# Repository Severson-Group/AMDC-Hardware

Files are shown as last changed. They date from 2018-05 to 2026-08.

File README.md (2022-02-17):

# Advanced Motor Drive Controller (AMDC) Hardware

*The Advanced Motor Drive Controller (AMDC) is an open-source project from the [Severson Research Group](https://severson.wempec.wisc.edu/) at [UW-Madison](http://www.engr.wisc.edu/department/electrical-computer-engineering/), affiliated with [Wisconsin Electric Machines and Power Electronics Consortium (WEMPEC)](https://wempec.wisc.edu/).*

Learn more at [docs.amdc.dev](https://docs.amdc.dev/).

---

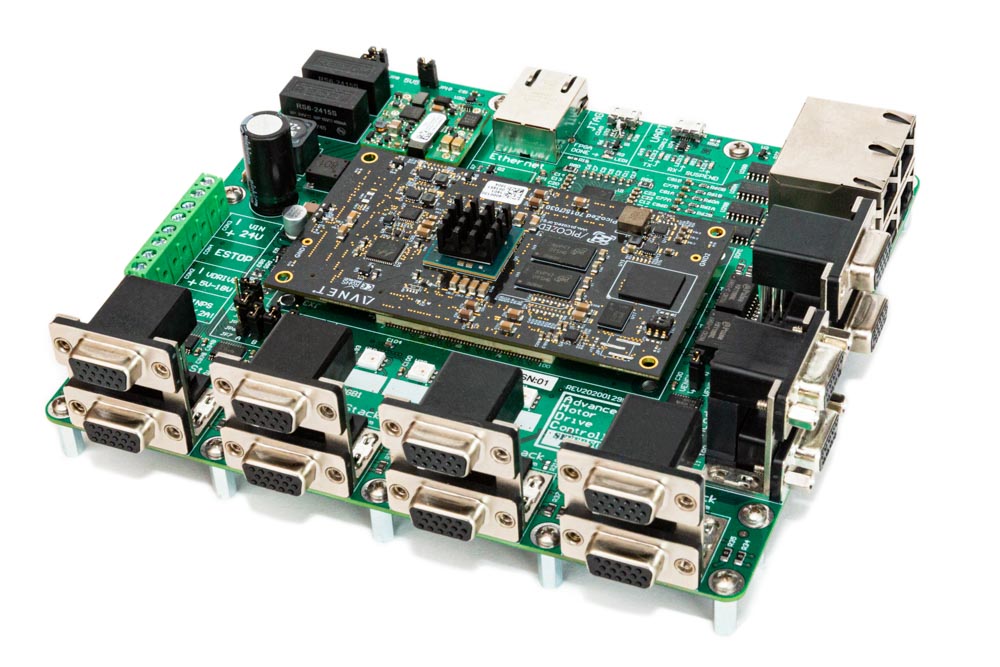
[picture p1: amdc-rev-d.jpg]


**AMDC-Hardware** is a collection of circuit board designs which are used to control advanced motor systems. The hardware design is open-source, modular, and research-oriented.

The flagship circuit board is the main AMDC (see latest design [here](https://github.com/Severson-Group/AMDC-Hardware/tree/develop/REV20210325E)) which is a carrier board for the [PicoZed System-on-Module](https://www.avnet.com/wps/portal/us/products/avnet-boards/avnet-board-families/picozed/). The PicoZed is a module itself which contains the core requirements for the [Xilinx Zynq-7000](https://www.xilinx.com/products/silicon-devices/soc/zynq-7000.html) System-on-Chip. The Xilinx Zynq-7000 SoC is a powerful processor with dual-core DSPs and a tightly integrated FPGA.

Extensive firmware support is provided in the [AMDC-Firmware](https://github.com/Severson-Group/AMDC-Firmware) repo which targets this architecture.

## Repository Structure

The `altium` directory contains all files pertaining to schematics / board design in Altium Designer. These files should be the latest working copy of the project.

The `REVyyyymmdd*` directories represent snapshots of the project that were used to produce a physical PCB. These directories contain the *Gerber*, *Drill* (Excellon format), *Bill of Materials* (CSV), and *Schematic* (PDF) files.
- `REV` indicates a revision of design for manufacturing
- `yyyymmdd` indicates the date on which design was frozen
- `*` (letter) indicates which revision in sequence (A - first, B - second, etc.)

### Accessory Boards

Numerous accessory circuit boards are designed to work with the AMDC (e.g., DAC, TestBoard, CAN expansion, I/O expansion).

These are located in the [`/Accessories/`](https://github.com/Severson-Group/AMDC-Hardware/tree/develop/Accessories) subfolder. Each accessory board follows the same repo set-up conventions as desribed above for the main AMDC.

## Interfaces

The AMDC is designed for research environments where flexible and plentiful I/O are required.

The provided interfaces include:
- 48 digital output channels (designed to provide PWM signals for 8 three phase, two level inverters)
- 8 analog input channels (+/- 10V differential input)
- 4 GPIO expansion ports (differential I/O)
- 2 quadrature encoder input

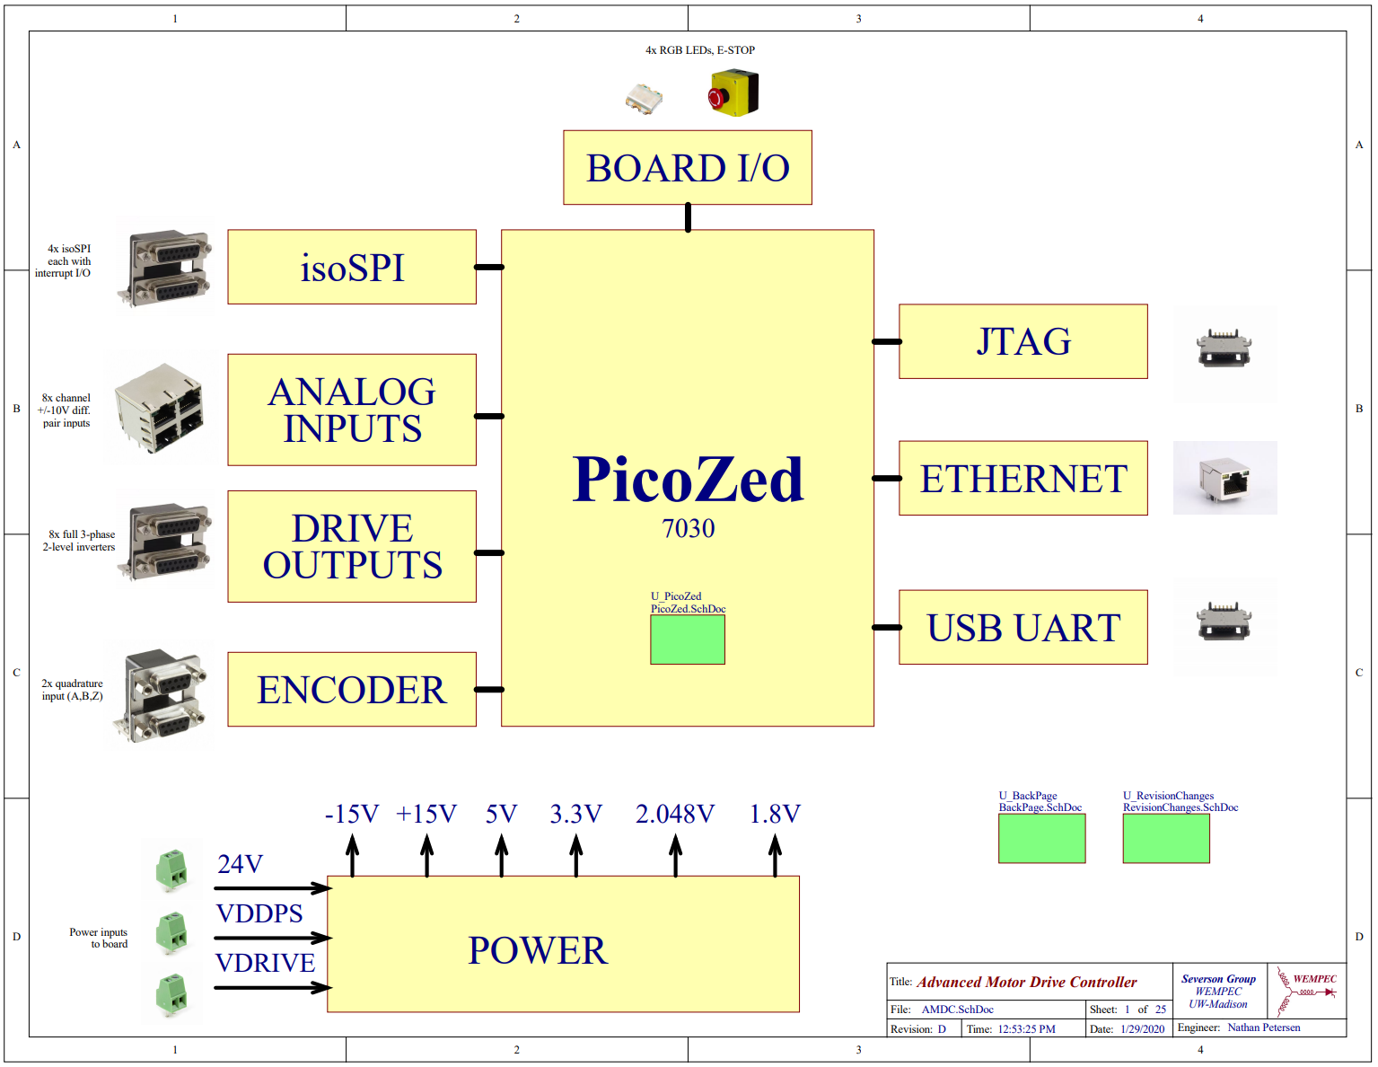
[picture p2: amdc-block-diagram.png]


## Getting Started

The AMDC-Hardware project is open-source -- contributors are welcome!

### Ordering Hardware

The `REVxxxx/` output folder contains the compiled design files needed to order hardware:
1. Review the board design using the 3D renderings and the schematics PDF
2. Check the `docs/` folder for any imformation about the board design
3. Order PCB blanks using the gerber files in the `REVxxxx/gerbers/` folder and the specs provided in the `README.md` file
4. Order components using the BOM file provided as CSV

### Designing Modifications

Note: all board designs are created using Altium Designer -- a license is required to design boards for the AMDC-Hardware project.

The `altium/` subfolder contains the latest design files for the board.

## Documentation

Detailed documentation about the hardware is available online at: [docs.amdc.dev/hardware](https://docs.amdc.dev/hardware/).

The documentation explains the design narrative and process, design choices, requirements, relevant equations and diagrams, etc.

## Background

This project originated as [Nathan Petersen's](https://github.com/npetersen2) Independent Study project during Spring 2018, advised by Prof. Eric Severson. It is now actively maintained by the [Severson Research Group](http://severson.wempec.wisc.edu/). Open source firmware is available on GitHub in the [AMDC-Firmware](https://github.com/Severson-Group/AMDC-Firmware) repository.

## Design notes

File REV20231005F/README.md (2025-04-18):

# AMDC REV20231010F

This folder contains the compiled design outputs for AMDC REV F. This includes the schematics, images of the PCB layout, the bill of materials (BOM), and the files needed to order fully populated boards from an online vendor.

## Board Parameters

| Question | Answer |
|---|---|
| Board Size | 6" x 6.75" |
| Numer of Layers | 6 Layers |
| Double Sided | Yes |
| Surface Finish | Tin Lead |
| Silkscreen | White |
| Material | FR-4, TG150 |
| Board Thickness | 1.6 mm |
| Min Trace Spacing | 0.15 mm (6 mil)  |
| Min Hole Size | 0.36 mm (14 mil) |
| Number of Holes | 1528 |
| Solder Mask | Green |
| HASL or ENIG | No |
| Finished Copper | 1 oz |

## Assembly Details

| Question[^1] | Answer |
|---|---|
| Unique Part Count[^2] | 67 |
| Number of Total Parts[^2] | 447 |
| Total SMT Part Count | 415 |
| Total Through-hole Part Count | 32 |
| Total Mechanical Screws | 13 |
| Total Mechanical Standoffs | 13 |
| Total Removable Jumpers | 10 |
| Total Picozed | 1 |
| BGA / QFN | Yes |

## Bill of Materials

The [Bill of Materials (BOM)](bom-rev-f.csv) contains components for 1 board. If users of this repo discover that any components are unvailable, please maintain an `alternate-components.md` file in this folder that lists approved alternates.

[^1]: For complete breakdown of surface mount, through-hole, and other components, see [this pull request comment](https://github.com/Severson-Group/AMDC-Hardware/pull/255#issuecomment-2815977355)

[^2]: This number does not include screws, standoffs, removable jumpers, or the picozed. With these components included, the unique part count is 71 and total parts is 484. Users are advised to not have their assembly vendor place these components.

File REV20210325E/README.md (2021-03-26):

# AMDC REV20210325E

This folder contains the compiled design outputs for AMDC REV E (design frozen on March 25, 2021). This includes the schematics, images of the PCB layout, the bill of materials (BOM), and the files needed to order fully populated boards from an online vendor.

## Board Parameters

| Question | Answer |
|---|---|
| Unique Part Count | 69 |
| Total Placements | 472 |
| Total SMT Part Count | 439 |
| Total SOP/QFP/QFN/BGA | 52 |
| Total Thru Hole Part Count | 32 |
| BGA / QFN | Yes |
| Double Sided | Yes |

| Question | Answer |
|---|---|
| Board Size (H x W) | 6" x 6.75"  |
| Numer of Layers | 6 |
| Number of Holes | 1519 |
| Number of Slots/Cutouts | 0 |
| Surface Finish | Tin Lead |
| Silkscreen | Both Sides  |
| Electrical Test | Yes |

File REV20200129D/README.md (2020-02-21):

# AMDC REV20200129D

This folder contains the compiled design outputs for AMDC REV D (design frozen on Jan 29, 2020). This includes the schematics, images of the PCB layout, the bill of materials (BOM), and the files needed to order fully populated boards from Screaming Circuits.

## How do I order more REV D AMDCs?

All the files required for placing an order of REV D AMDCs reside in this folder. The following steps outline the ordering procedure with answers to the questions asked by Screaming Circuits. We will assume ordering 10 qty.

1. Go to [Screaming Circuits website](https://www.screamingcircuits.com/).
2. Start a new online quote.
3. Fill out `Assembly Quote` section

| Question | Answer |
|---|---|
| Quantity | 10 |
| Unique Part Count | 64 |
| Total Placements | 366 |
| Thru Hole Placements | 27 |
| BGA / QFN | Yes |
| Double Sided | Yes, SMT |
| RoHS | No |
| Class III | No |
| ITAR | No |

4. Fill out `PCB Fabrication Quote` section

| Question | Answer |
|---|---|
| Board Size (H x W) | 6" x 6.75"  |
| Numer of Layers | 6 |
| Number of Holes | 1387 |
| Number of Slots/Cutouts | 0 |
| Surface Finish | Tin Lead |
| Silkscreen | Both Sides  |
| Electrical Test | Yes |

5. Fill out `Parts Quote` section
    1. Upload the BOM from the `ScreamingCircuits/` folder.
    2. Wait for website to parse file... takes ~1 minute...
    3. Look for parts that they cannot source (out of stock, etc) -- this is usually fine, but make sure!
    3. Click `SAVE CHANGES`.

6. Select `Pricing` option and click `CHECK OUT`.
7. Name the project: "AMDC" and "REV20200129D" are logical.
8. Upload a ZIP file of the `ScreamingCircuits` folder for the "Project Files" section.
9. Fill out contact info, shipping info, and billing info.
10. Pay for order and wait for AMDCs to arrive!

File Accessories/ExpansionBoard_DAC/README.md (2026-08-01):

# AMDC DAC Expansion Board

The AMDC DAC expansion board is an accessory for the AMDC Rev E which provides 8 analog outputs (+- 10V output). The expansion board plugs into the AMDC via the Power Stack or GPIO interfaces.

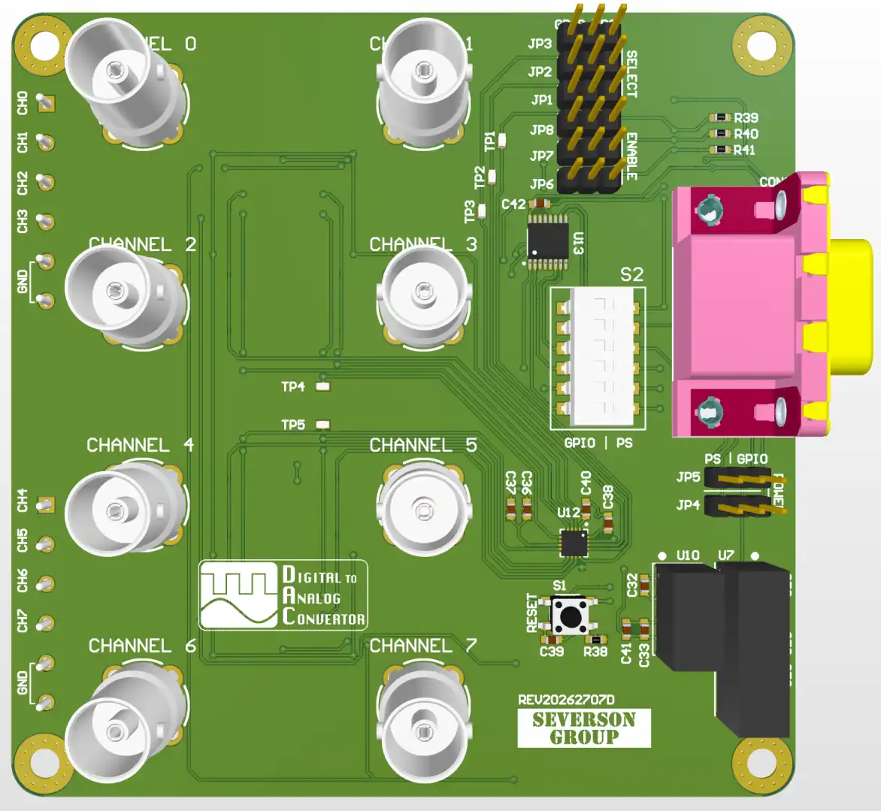
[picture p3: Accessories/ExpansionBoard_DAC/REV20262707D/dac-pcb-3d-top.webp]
PCD_3D


## Documentation

Documentation about the design of this expansion board is located at [docs.amdc.dev/accessories/dac/](https://docs.amdc.dev/main/accessories/dac/index.html).

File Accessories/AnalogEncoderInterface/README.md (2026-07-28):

# Analog Encoder Interface Board

This subfolder houses all the design files for the Analog Encoder Interface board. This board plugs into the AMDC analog inputs via ethernet cables.

## Documentation

Read about the design of this board on [docs.amdc.dev](docs.amdc.dev/main/accessories/analog-encoder).

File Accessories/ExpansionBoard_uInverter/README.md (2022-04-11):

# uInverter Board

The uInverter (micro-inverter) board is an accessory for the AMDC. The purpose of this board is to serve as a low-cost, micro-level prototype board to demonstrate three-phase current regulation using the AMDC. It uses a 12V DC supply to drive a three phase RL load circuit to emulate a motor.   

## Features:    
- Three phase AC current and DC bus voltage sensing feedback to AMDC.   
- Test points to measure voltages at various locations in the supply as well as load circuits.   
- BNC connector to directly measure the current waveforms on an oscilloscope conveniently.    

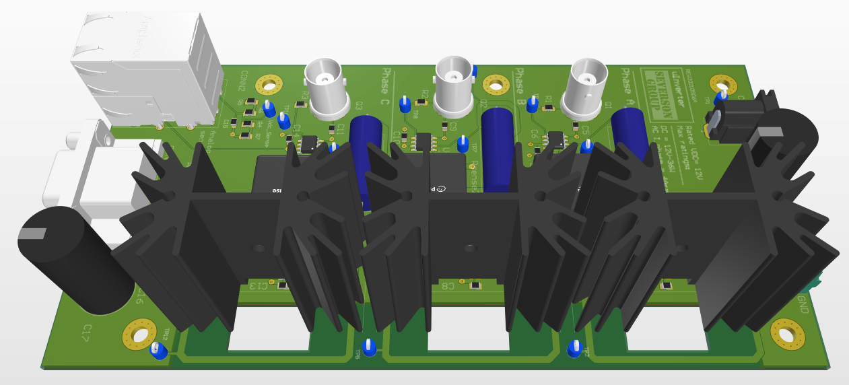
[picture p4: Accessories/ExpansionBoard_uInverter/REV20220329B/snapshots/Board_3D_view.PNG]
PCB 3D


## Documentation

Detailed documentation about the uInverter board is available online at: [docs.amdc.dev/accessories/uinverter](https://docs.amdc.dev/accessories/uinverter/index.html).

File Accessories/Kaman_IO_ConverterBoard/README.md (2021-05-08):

# Kaman IO Converter Board

The Kaman I/O Converter board is an accessory for the AMDC Rev D which converts the 4 differential I/O from the IsoSPI port on the AMDC to single ended I/O specifically for the Kaman KD-5690-FE eddy current sensor. The converter board plugs into the AMDC via the IsoSPI interface. 

## Documentation

Documentation about the design of this board is located in then [docs folder.](docs/)

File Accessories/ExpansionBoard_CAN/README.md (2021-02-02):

# AMDC CAN Expansion Board

The AMDC CAN expansion board is an accessory to the AMDC REVD with the goal of providing the AMDC the ability to interface with CAN devices. 

## Documentation
Documentation about the design of this expansion board can be found in the [docs folder.](docs/)

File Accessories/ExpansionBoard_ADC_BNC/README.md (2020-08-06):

# AMDC Expansion Board: Analog Inputs to BNC

This subfolder houses all the design files for the AMDC analog to BNC expansion board. This board plugs into the AMDC analog inputs via four ethernet cables.

## Documentation

Read about the design of this board in the [`docs/` folder](docs/).

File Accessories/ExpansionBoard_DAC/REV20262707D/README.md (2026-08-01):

# AMDC DAC Expansion Board REV20262707D

This folder contains the compiled design outputs for the AMDC DAC Expansion Board REV D. This includes the schematics, images of PCB layout, the bill of materials (BOM), and the files needed to order PCBs from online vendors.

## Board Parameters

| Question | Answer |
|---|---|
| Board Size | 3.91" x 3.91" |
| Number of Layers | 2 Layers |
| Double Sided | Yes |
| Surface Finish | Tin lead |
| Silkscreen | White (both sides) |
| Material | FR-4 |
| Board Thickness | 1.6 mm |
| Min Trace Spacing | 0.152 mm (6 mil) |
| Min Hole Size | 0.36 mm (14 mil) |
| Number of Holes | 233 |
| Solder Mask | Green |
| HASL or ENIG | HASL |
| Finished Copper | 1 oz |

## Assembly Details

| Question | Answer |
|---|---|
| Unique Part Count[^1] | 27 |
| Number of Total Parts[^1] | 117 |
| Total SMT Part Count | 96 |
| Total Through-hole Part Count | 21 |
| Total Mechanical Screws | 4 |
| Total Mechanical Standoffs | 4 |
| Total Jumper Connectors | 8 |
| BGA / QFN | QFN (U12) |

## Bill of Materials

The [Bill of Materials (BOM)](./dac-rev-d-bom.csv) contains components for 1 board. If users of this repo discover that any components are unavailable, please maintain an `alternate-components.md` file in this folder that lists approved alternates.

[^1]: This number does not include screws, standoffs, or jumper connectors. With screws, standoffs, and jumper connectors included, the unique part count is 30 and total parts is 133. Users are advised to not have their assembly vendor place screws, standoffs, and jumper connectors.

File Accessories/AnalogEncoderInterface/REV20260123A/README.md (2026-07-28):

# Analog Encoder Interface Board REV20260123A
This folder contains the compiled design outputs for the Analog Encoder Interface Board REVA. This includes the schematics, images of PCB layout, the bill of materials (BOM), and the files needed to order PCBs from online vendors.

## Analog Encoder Interface Board

| Question | Answer |
|---|---|
| Board Size | 73mm x 80mm |
| Number of Layers | 4 Layers |
| Double Sided | Yes |
| Surface Finish | Tin Lead |
| Silkscreen | White |
| Material | FR-4, TG150 |
| Board Thickness | 1.6 mm (62 mil) |
| Min Trace Spacing | 0.2 mm (7.9 mil)  |
| Min Hole Size | 0.3 mm (11.8 mil) |
| Number of Holes | 63 |
| Solder Mask | Purple |
| HASL or ENIG | No |
| Inner Copper | 1 oz |
| Outer Copper | 1 oz |

### Assembly Details

| Question | Answer |
|---|---|
| Unique Part Count | 20 |
| Number of Total Parts | 57 |
| Total SMD Part Count | 24 |
| Total Through-hole Part Count  | 25 |
| Total Mechanical Screws | 4 |
| Total Mechanical Standoffs | 4 |
| BGA / QFN | No |

## Bill of Materials

The [Bill of Materials (BOM)](aei-bom.csv) contains components for 1 of each board.

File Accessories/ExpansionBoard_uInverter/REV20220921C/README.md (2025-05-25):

# uInverter Board

This folder contains the compiled design outputs for the uInverter expansion board. This includes schematics, images of the PCB layout, the bill of materials (BOM) and the files needed to order boards from an online vendor. 

## Board Parameters

| Question | Answer |
|---|---|
| Board Size | 3.5" x 6.9" |
| Number of Layers  | 2 Layers |
| Double Sided | No |
| Surface Finish | Tin lead |
| Silkscreen | White |
| Material | FR-4, TG150 |
| Board Thickness | 1.6mm |
| Min Track/Spacing | 0.15 mm (6 mil) |
| Min Hole Size | 0.38 mm (15 mil)  |
| Number of holes | 198 |
| Solder Mask | Black |
| HASL or ENIG | No |
| Finished Copper | 1 oz |

## Assembly Details

| Question | Answer |
|---|---|
| Unique Part Count[^1] | 19 |
| Number of Total Parts[^1] | 61 |
| Total SMT Part Count | 33 |
| Total Through-hole Part Count | 28 |
| Total Mechanical Components | 28 |
| BGA / QFN | No |

## Bill of Materials

The [Bill of Materials (BOM)](uinv-rev-c-bom.csv) contains components for 1 board. If users of this repo discover that any components are unavailable, please maintain an `alternate-components.md` file in this folder that lists approved alternates.

[^1]: This number does not include mechanical components. With mechanical components included, the unique part count is 27 and total parts is 89. Users are advised to not have their assembly vendor place screws and standoffs.

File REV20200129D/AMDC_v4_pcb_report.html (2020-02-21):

Altium customize

# Board Information Report

Date: | | 1/29/2020
Time: | | 1:09:38 PM
Elapsed Time: | | 00:00:01
Filename: | | C:\Users\Nathan\Documents\GitHub\AMDC-Hardware\altium\PCB_v4.PcbDoc
Units: | | mmmils

## Contents

Contents

Board Specification

General

Routing

Routing Information

Layer Information

Layer Information

Drill Pairs

Board Holes

Non-Plated Hole Size

Plated Hole Size

Board Slots

Non-Plated Slot Size

Plated Slot Size

Board Square Holes

Non-Plated Square Hole Size

Plated Square Hole Size

Other

Top Layer Annular Ring Size

Mid Layer Annular Ring Size

Bottom Layer Annular Ring Size

Pad Solder Mask

Pad Paste Mask

Pad Pwr/Gnd Expansion

Pad Relief Conductor Width

Pad Relief Air Gap

Pad Relief Entries

Via Solder Mask

Via Pwr/Gnd Expansion

Track Width

Arc Line Width

Arc Radius

Arc Degrees

Text Height

Text Width

Net Track Width

Net Via Size

## Board Specification

General
Board Size | 6750mils x 6000mils
Components on board | 408

Back to top

## Routing

Routing Information
Routing completion | 100.00%
Connections | 1700
Connections routed | 1700
Connections remaining | 0

Back to top

## Layer Information

Layer | Arcs | Pads | Vias | Tracks | Texts | Fills | Regions | ComponentBodies
Top Layer | 11 | 960 | 0 | 2439 | 0 | 0 | 140 | 0
Int1 (GND) | 0 | 0 | 0 | 0 | 0 | 0 | 1 | 0
Int2 (Sign) | 276 | 0 | 0 | 1094 | 0 | 0 | 0 | 0
Int3 (Sign) | 0 | 0 | 0 | 703 | 0 | 0 | 0 | 0
Int4 (PWR) | 0 | 0 | 0 | 192 | 0 | 0 | 1 | 0
Bottom Layer | 10 | 907 | 0 | 2742 | 0 | 0 | 159 | 0
Mechanical 15 | 0 | 0 | 0 | 569 | 0 | 0 | 0 | 6
Mechanical 13 | 46 | 0 | 0 | 384 | 0 | 0 | 0 | 81
Mechanical 12 | 0 | 0 | 0 | 20 | 0 | 0 | 0 | 11
Mechanical 1 | 1 | 0 | 0 | 0 | 0 | 0 | 0 | 277
Multi-Layer | 0 | 489 | 898 | 0 | 0 | 0 | 1 | 0
Drill Guide | 0 | 0 | 0 | 0 | 0 | 0 | 0 | 0
Keep-Out Layer | 4 | 0 | 0 | 4 | 0 | 0 | 0 | 0
Drill Drawing | 0 | 0 | 0 | 0 | 0 | 0 | 0 | 0
Top Paste | 0 | 0 | 0 | 0 | 0 | 0 | 0 | 0
Top Overlay | 44 | 0 | 0 | 6536 | 511 | 4 | 1 | 0
Top Solder | 0 | 0 | 0 | 0 | 0 | 0 | 0 | 0
Bottom Solder | 0 | 0 | 0 | 0 | 0 | 0 | 0 | 0
Bottom Overlay | 61 | 0 | 0 | 325 | 403 | 0 | 0 | 0
Bottom Paste | 0 | 0 | 0 | 0 | 0 | 0 | 0 | 0
Total | 453 | 2356 | 898 | 15008 | 914 | 4 | 303 | 375

Back to top

Drill Pairs | Vias
Top Layer - Bottom Layer | 898
Total | 898

Back to top

## Board Holes

Non-Plated Hole Size | Pads | Vias
32.008mils | 3 | 0
47.992mils | 3 | 0
Total | 6 | 0

Back to top

Plated Hole Size | Pads | Vias
0mils | 1867 | 0
12mils | 156 | 0
13.5mils | 0 | 7
14mils | 0 | 809
20mils | 0 | 79
30mils | 0 | 2
35mils | 32 | 0
35.039mils | 12 | 0
39.016mils | 2 | 0
39.37mils | 16 | 0
40mils | 0 | 1
40.158mils | 25 | 0
43.307mils | 18 | 0
44mils | 150 | 0
47.244mils | 6 | 0
50mils | 5 | 0
50.984mils | 2 | 0
51.181mils | 8 | 0
62mils | 6 | 0
125mils | 4 | 0
125.984mils | 4 | 0
126mils | 20 | 0
127.953mils | 2 | 0
128mils | 2 | 0
150mils | 13 | 0
Total | 2350 | 898

Back to top

## Board Slots

Non-Plated Slot Size / Length | Pads
Total | 0

Back to top

Plated Slot Size / Length | Pads
Total | 0

Back to top

## Board Square Holes

Non-Plated Square Hole Size | Pads
Total | 0

Back to top

Plated Square Hole Size | Pads
Total | 0

Back to top

## Other

Top Layer Annular Ring Size | Count
-2.008mils | 3
-2.008mils | 3
-0.047mils | 2
0mils | 2
12mils | 809
12.5mils | 7
14.961mils | 12
18mils | 156
19.685mils | 18
19.843mils | 25
20mils | 229
20.984mils | 2
23.622mils | 16
25mils | 32
26.583mils | 4
27.559mils | 8
27.756mils | 2
30mils | 2
39.37mils | 4
40mils | 8
45mils | 4
47.244mils | 6
54mils | 20
150mils | 13
Total | 1387

Back to top

Mid Layer Annular Ring Size | Count
-2.008mils | 3
-2.008mils | 3
-0.047mils | 2
0mils | 2
12mils | 809
12.5mils | 7
14.961mils | 12
18mils | 156
19.685mils | 18
19.843mils | 25
20mils | 229
20.984mils | 2
23.622mils | 16
25mils | 32
26.583mils | 4
27.559mils | 8
27.756mils | 2
30mils | 2
39.37mils | 4
40mils | 8
45mils | 4
47.244mils | 6
54mils | 20
150mils | 13
Total | 1387

Back to top

Bottom Layer Annular Ring Size | Count
-2.008mils | 3
-2.008mils | 3
-0.047mils | 2
0mils | 2
12mils | 809
12.5mils | 7
14.961mils | 12
18mils | 156
19.685mils | 18
19.843mils | 25
20mils | 229
20.984mils | 2
23.622mils | 16
25mils | 32
26.583mils | 4
27.559mils | 8
27.756mils | 2
30mils | 2
39.37mils | 4
40mils | 8
45mils | 4
47.244mils | 6
54mils | 20
150mils | 13
Total | 1387

Back to top

Pad Solder Mask | Count
1.969mils | 53
2mils | 64
2.5mils | 2201
2.953mils | 25
19.685mils | 13
Total | 2356

Back to top

Pad Paste Mask | Count
0mils | 2356
Total | 2356

Back to top

Pad Pwr/Gnd Expansion | Count
10mils | 2356
Total | 2356

Back to top

Pad Relief Conductor Width | Count
6mils | 2356
Total | 2356

Back to top

Pad Relief Air Gap | Count
6mils | 2356
Total | 2356

Back to top

Pad Relief Entries | Count
4 | 2356
Total | 2356

Back to top

Via Solder Mask | Count
2.5mils | 898
Total | 898

Back to top

Via Pwr/Gnd Expansion | Count
10mils | 898
Total | 898

Back to top

Track Width | Count
0.5mils | 4571
1mils | 1454
1.969mils | 320
3.937mils | 608
6mils | 3530
7mils | 2
7.874mils | 310
8mils | 347
10mils | 2567
12mils | 242
19.685mils | 1
20mils | 376
30mils | 515
40mils | 2
50mils | 129
75mils | 15
80mils | 16
100mils | 3
Total | 15008

Back to top

Arc Line Width | Count
3.937mils | 60
4mils | 8
8mils | 276
9.843mils | 60
10mils | 11
12mils | 4
18mils | 4
19.685mils | 1
23.622mils | 29
Total | 453

Back to top

Arc Radius | Count
1.969mils | 1
4.6mils | 8
4.921mils | 60
5.4mils | 144
6mils | 4
9mils | 17
9.843mils | 1
10.8mils | 12
11.811mils | 29
15.748mils | 1
19.685mils | 45
28.8mils | 12
30.067mils | 43
30.366mils | 1
31.441mils | 1
39.37mils | 13
48.067mils | 40
48.366mils | 1
49.441mils | 1
57.554mils | 1
80mils | 4
150mils | 8
175mils | 4
250mils | 2
Total | 453

Back to top

Arc Degrees | Count
0 | 2
1 | 1
23 | 2
32 | 11
45 | 1
68 | 1
70 | 1
72 | 2
75 | 1
76 | 2
77 | 36
90 | 178
91 | 2
113 | 2
121 | 1
122 | 9
132 | 1
139 | 1
142 | 1
145 | 3
150 | 1
154 | 21
176 | 1
360 | 172
Total | 453

Back to top

Text Height | Count
15mils | 1
30mils | 18
40mils | 428
50mils | 19
60mils | 428
70mils | 1
80mils | 16
125mils | 1
393.701mils | 2
Total | 914

Back to top

Text Width | Count
4mils | 1
5mils | 18
6mils | 12
10mils | 845
12mils | 8
15mils | 24
20mils | 6
Total | 914

Back to top

Net Track Width | Count
6mils | 461
10mils | 44
Total | 505

Back to top

Net Via Size | Count
22mils | 505
Total | 505

Back to top

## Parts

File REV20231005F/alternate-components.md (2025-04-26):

# Alternate Components

**A table of acceptable replacement components for the AMDC REV20231005F**

##

| Designator | Description | Original Part Number | Approved Alternate Part Numbers |
|---|---|---|---|
| HEATSINK1 | Heat Sink BGA Aluminum Top Mount | [1528-1697-ND](https://www.digikey.com/en/products/detail/adafruit-industries-llc/3083/6058478) | [684-ATS014014007-SF-3F-ND](https://www.digikey.com/en/products/detail/advanced-thermal-solutions-inc/ATS014014007-SF-3F/18711115) |
| C80 | CAP ALUM 100UF 20% 35V SMD | [493-2203-6-ND](https://www.digikey.com/en/products/detail/nichicon/UWT1V101MCL1GS/589944) | [493-6338-1-ND](https://www.digikey.com/en/products/detail/nichicon/UWZ1V101MCL1GS/2550909) |
| U7 | DC DC CONVERTER 24V 6W | [102-PQQ6W-Q24-S24-S-ND](https://www.digikey.com/en/products/detail/cui-inc/PQQ6W-Q24-S24-S/13402043) | [2725-URB2424S-6WR3-ND](https://www.digikey.com/en/products/detail/mornsun-america-llc/URB2424S-6WR3/13168170) <br> [4457-PDL06-24S24W-ND](https://www.digikey.com/en/products/detail/p-duke-technology/PDL06-24S24W/13531900) |
| Q3 | MOSFET 2N-CH 60V 5.3A 8SOIC | [SI4946CDY-T1-GE3DKR-ND](https://www.digikey.com/en/products/detail/vishay-siliconix/SI4946CDY-T1-GE3/7915484)| [SI4900DY-T1-GE3CT-ND](https://www.digikey.com/en/products/detail/vishay-siliconix/SI4900DY-T1-GE3/2622306) <br> [SI9945BDY-T1-GE3CT-ND](https://www.digikey.com/en/products/detail/vishay-siliconix/SI9945BDY-T1-GE3/2622740) |
| U18 | IC REG LINEAR 15V 500MA DPAK | [MC78M15CDTRKGOSCT-ND](https://www.digikey.com/en/products/detail/onsemi/MC78M15CDTRKG/919383) | [MC78M15ACDTRKG](https://www.digikey.com/en/products/detail/onsemi/MC78M15ACDTRKG/1481479) |

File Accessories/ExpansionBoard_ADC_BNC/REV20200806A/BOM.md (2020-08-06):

| Comment | Description | Designator | Quantity | Supplier Part Number 1 | Supplier Order Qty 1 |
|-|-|-|-|-|-|
| RJSAE538004 | CONN MOD JACK 8P8C R/A SHIELDED | CON1 | 1 | RJSAE538004-ND | 5 |
| 1935200 | TERM BLK 6POS SIDE ENTRY 5MM PCB | CON2 | 1 | 277-1581-ND | 5 |
| 5-1634503-1 | BNC Connector Jack, Female Socket 50 Ohm Through Hole Solder | Q1, Q2, Q3, Q4, Q5, Q6, Q7, Q8 | 8 | A97581-ND | 40 |
| Screw-4-40 |  | SCREW1, SCREW2, SCREW3, SCREW4 | 4 | KEY1046-ND | 20 |
| Standoff-4-40 |  | STANDOFF1, STANDOFF2, STANDOFF3, STANDOFF4 | 4 | 36-1656-ND | 20 |
| Test Point | Test Point | TP1, TP2, TP3, TP4, TP5, TP6, TP7, TP8, TP9, TP10, TP11, TP12, TP13, TP14, TP15, TP16 | 16 | 36-5007-ND | 80 |

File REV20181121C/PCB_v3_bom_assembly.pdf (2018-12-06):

Designator | Supplier Part Number 1 | Comment | Description | Quantity | Footprint | Manufacturer | Capacitance | Colour | Resistance | Tolerance | Voltage | Voltage Rating | Voltage Rating (DC)
C1, C6, C11, C15, C24, C31, C37, C43, C48 | 1276-1909-6-ND | Capacitor | Capacitor | 9 | 0603-CAP | Samsung | 100pF | | | 10% | | 50V

C2, C4, C5, C7, C9, C10, C12, C14, C16, C18,
C25, C27, C28, C32, C34, C35, C38, C40, C44, C46, C50, C51, C52, C54, C55, C56, C57, C58, C59, C60, C63, C64, C67, C68, C71, C72, C75, C76, C79, C80, C83, C84, C85, C86, C91A, C91B, C91C, C91D, C91E, C91F, C92A, C92B, C92C, C92D, C92E, C92F, C93A, C93B, C93C, C93D, C93E, C93F, C93G, C93H, C93I, C93J, C93K, C93L, C93M, C93N, C93O, C93P, C94A, C94B, C94C, C94D, C94E, C94F, C94G, C94H, C94I, C94J, C94K, C94L, C94M, C94N, C94O, C94P, C95A, C95B, C95C, C95D, C95E, C95F, C96A, C96B, C96C, C96D, C96E, C96F, C97A, C97B, C97C, C97D, C97E, C97F, C98A, C98B, C98C, C98D, C98E,
C98F, C99A, C99B, C99C, C99D, C99E, C99F,
C100A, C100B, C100C, C100D, C100E,
C100F, C172, C174, C176 | 1276-1012-6-ND | Capacitor | Capacitor | 127 | 0603-CAP | Samsung | 100nF | 80% | 50V | 50V
C3, C8, C13, C17, C20, C21, C22, C26, C29, C30, C33, C36, C39, C41, C45 | 1276-1119-6-ND | Capacitor | Capacitor | 15 | 0603-CAP | Samsung | 10uF | | 20% | 6.3V | 6.3V
C19, C157A, C157B, C158A, C158B, C161, C162, C163A, C163B, C164A, C164B | 1276-1192-6-ND | Capacitor | Capacitor | 11 | 0603-CAP | Samsung | 10uF | | 10% | 6.3V, [NoParam] | 10V | 10V
C23, C42, C47, C53, C61, C62, C65, C66, C69, C70, C73, C74, C77, C78, C81, C82, C89A, C89B, C89C, C89D, C89E, C89F, C89G, C89H, C89I, C89J, C89K, C89L, C89M, C89N, C89O, C89P, C90A, C90B, C90C, C90D, C90E, C90F, C90G, C90H, C90I, C90J, C90K, C90L, C90M, C90N, C90O, C90P, C179A, C179B, C179C, C179D, C180A, C180B, C180C, C180D, C183A, C183B, C183C, C183D, C184A, C184B, C184C, C184D, C187A, C187B, C187C, C187D, C188A, C188B, C188C, C188D | 1276-6524-6-ND | Capacitor | Capacitor | 72 | 0603-CAP | Samsung | 1uF | | 20% | | 16V
C87, C105, C109, C110, C112, C113 | 709-1046-6-ND | Capacitor | Capacitor | 6 | 1808-CAP | Johanson | 1nF | | 10% | | 2kV | 2kV
C88, C115, C116 | 445-9015-6-ND | Capacitor | Capacitor | 3 | 0603-CAP | TDK | 10uF | | 20% | | 25V | 25V
C101 | 493-2203-6-ND | Cap Pol1 | Polarized Capacitor (Radial) | 1 | CAP -UWT1V101MCL1GS | Nichicon | 100uF | | 20% | 35V | 35V | 35V
C102, C103, C104 | 493-12786-1-ND | Cap Pol1 | Polarized Capacitor (Radial) | 3 | CAP -UVR1H102MHD1TO | Nichicon | 1000uF | | 20% | 50V | 50V | 50V
C106, C107, C108, C111, C114 | 445-3919-6-ND | Capacitor | Capacitor | 5 | 1812-CAP | TDK | 6.8uF | | 10% | 50V | 50V | 50V
C165A, C165B, C166A, C166B, C167A, C167B, C168A, C168B, C169, C173, C175 | 490-10486-6-ND | Capacitor | Capacitor | 11 | 0603-CAP | Murata | 2.2uF | | 20% | | 35V | 35V
C170 | 445-7743-6-ND | Capacitor | Capacitor | 1 | 1812-CAP | TDK | 100uF | | 20% | | 10V | 10V
C171 | 1276-6504-6-ND | Capacitor | Capacitor | 1 | 0603-CAP | Samsung | 22uF | | 20% | | 10V
C181A, C181B, C181C, C181D, C182A, C182B, C182C, C182D, C185A, C185B, C185C, C185D, C186A, C186B, C186C, C186D | 478-1548-6-ND | Capacitor | Capacitor | 16 | 0603-CAP | Kyocera AVX | 33nF | | 10% | 50V | 50V | 50V
CON1 | A115463-ND | 5569257-1 | CONN MOD JACK 8P8C R/A SHIELDED | 1 | 5569257-1 | TE Connectivity
CON2, CON3, CON4 | 277-1667-ND | ScrewTerminal_1x2 | | 3 | 1935161 | Phoenix Contact | | | | | 300V
CON5 | AE10921-ND | A-DF 09 A/KG-T2S | CONN D-SUB RCPT 9POS R/A SOLDER | 1 | A-DF 09 A/KG-T2S | Assmann
CON6 | 380-1110-ND | L829-1J1T-43 | | 1 | L829-1J1T-43 | Bel | | Green,Orange,Y ellow,Silver
CON7, CON8A, CON8B, CON8C, CON8D | 1115FFE-ND | 178-015-513R571 | CONN D-SUB RCPT 15POS R/A SLDR | 5 | 178-015-513R571 | NorComp | | Black

Designator | Supplier Part Number 1 | Comment | Description | Quantity | Footprint | Manufacturer | Capacitance | Colour | Resistance | Tolerance | Voltage | Voltage Rating | Voltage Rating (DC)
CON9 | 1286-1192-ND | JTAG-SMT2 | | 1 | JTAG-SMT2 | Digilent
CON10 | 609-3243-ND | JTAG | | 1 | PIN_HEADER_2x7 | Amphenol FCI | | Black | | | | 1.5kV
CON11, CON12 | A97799TR-ND | 1981584-1 | CONN RCPT MICRO USB TYPE AB | 2 | 1981584-1 | TE Connectivity | | Grey | | | | 30V
CON13 | 609-3391-ND | PIN_2x4 | | 1 | PIN_HEADER_2x4 | Amphenol FCI | | Black | | | | 1.5kV
CON14 | 609-3218-ND | PIN_2x3 | | 1 | PIN_HEADER_2x3 | Amphenol FCI | | Black | | | | 1.5kV
CON15, CON16 | 609-3390-ND | PIN_2x2 | | 2 | PIN_HEADER_2x2
D1, D7, D8 | F2895TR-ND | SP1001-04JTG | TVS DIODE 5.5V 13V SC70-5 | 3 | SC70-5 | [NoParam], Littelfuse | [NoParam], 8pF
D2 | RB521S30T1GOSTR-ND | RB521 | DIODE SCHOTTKY 30V 200MA SOD523 | 1 | SOD-523 | ON Semiconductor | | | | | | | 30V
D3 | F2895DKR-ND | SP1001-04JTG | TVS DIODE 5.5V 13V SC70-5 | 1 | SC70-5 | Littelfuse | 8pF
D5A, D5B, D5C, D5D, D6A, D6B, D6C, D6D, D9A, D9B, D9C, D9D, D10A, D10B, D10C, D10D | SMAJ22CABDKR-ND | TVS SMAJ22CA | TVS DIODE 22V 35.5V SMA | 16 | SMA | Bourns
JP1, JP9, JP10, JP12, JP13, JP14 | 732-5315-ND | Jumper2 | | 6 | PIN_HEADER_1x2 | Wurth Electronics | | Black | | | | 250V
JP2, JP3, JP4, JP5, JP8, JP11, JP16 | 732-5316-ND | Jumper3 | | 7 | PIN_HEADER_1X3 | Wurth Electronics | | Black
JP6, JP7, MH1, MH2, MH3, MH4, MH5, MH6, MH7, MH8, MH9, MH10, MH11, SOM1 | | Jumper4T, MOUNT_HOLE, PicoZed | [NoValue], MOUNTING HOLE, PicoZed SOM Carrier Footprint | 14 | PIN_HEADER_1X3T, MOUNTING_HOLE, PicoZedSOM
L1 | SRP1770TA-101MDKR-ND | IND SRP1770TA-101M | FIXED IND 100UH 5.3A 118 MOHM | 1 | IND - SRP1770TA-101M | Bourns | | | | 20%
L2 | 732-2215-6-ND | CMC 744273801 | CMC 450UH 6.5A 2LN TH | 1 | CMC 744273801 | Wurth Electronics | | | 11mR | 25% | | | 80V
LED1, LED5 | 160-1448-6-ND | LED | | 2 | 0603-LED | Vishay Lite-On | | Yellow
LED2 | 160-1447-6-ND | LED | | 1 | 0603-LED | Vishay Lite-On | | Red | | | 2V
LED3 | 160-1446-6-ND | LED | | 1 | 0603-LED | Vishay Lite-On | | Green
LED4 | 492-1243-2-ND | LED_RGB_CA | | 1 | 1210-LED-RGB-CA
LED6 | 160-1446-2-ND | LED | | 1 | 0603-LED | Vishay Lite-On | | Green
LED7 | 160-2212-6-ND | LED | | 1 | 0603-LED | Vishay Lite-On | | Blue | | | 29V
Q1, Q2, Q3, Q4, Q5 | DMN65D8L-7DIDKR-ND | MOSFET | | 5 | SOT95P250-3N | Diodes
Q6, Q7, Q8 | DMN65D8L-7DITR-ND | MOSFET | | 3 | SOT95P250-3N | Diodes
Q9 | SI4946CDY-T1-GE3DKR-ND | Si4946 | MOSFET Dual N-Channel 60V SO-8 Dual | 1 | SO8_N | Vishay
R1, R23, R24, R25, R26A, R26B, R26C, R26D, R46, R53 | P0.0GDKR-ND | Resistor | Resistor | 10 | 0603-RES | Panasonic | | | 0mR, 0R | 0% | | 75V | 50V
R2, R30 | RMCF0603FT49K9DKR-ND | Resistor | Resistor | 2 | 0603-RES | Stackpole Electronics | | | 49.9k | 1%
R3 | 311-23.7KHRDKR-ND | Resistor | Resistor | 1 | 0603-RES | Yageo | | | 23.7k | 1% | | 75V | 50V
R4, R6 | RMCF0603FT60K4CT-ND | Res | Resistor | 2 | 0603-RES | Stackpole Electronics | | | 60.4k | 1%
R5 | RMCF0603FT3M92CT-ND | Res | Resistor | 1 | 0603-RES | Stackpole Electronics | | | 3.92M | 1%
R7 | RMCF0603FT40K2CT-ND | Res | Resistor | 1 | 0603-RES | Stackpole Electronics | | | 40.2k | 1%
R10, R11, R14, R15, R16 | P240HDKR-ND | Resistor | Resistor | 5 | 0603-RES | Panasonic | | | 240R | 1% | | 75V | 75V
R12 | YAG3628DKR-ND | Resistor | Resistor | 1 | 0603-RES | Yageo | | | 750 | 1% | | 50V
R13, R19, R27, R28, R29, R31, R32, R52, R57A, R57B, R57C, R57D, R58A, R58B, R58C, R58D, R59A, R59B, R59C, R59D, R60A, R60B, R60C, R60D | YAG3561DKR-ND | Resistor | Resistor | 24 | 0603-RES | Yageo | | | 100R, 100 | 1% | | 50V
R17, R18, R21, R22 | P10.0KHCT-ND | Resistor | Resistor | 4 | 0603-RES | Panasonic | | | 10kR | 1% | | 75V | 75V
R38A, R38B | 311-115KHRDKR-ND | Resistor | Resistor | 2 | 0603-RES | Yageo | | | 115k | 1% | | 50V | 50V
R39A, R39B, R43, R44, R45, R47, R48, R50, R51 | P10.0KHDKR-ND | Resistor | Resistor | 9 | 0603-RES | Panasonic | | | 10kR | 1% | | 75V | 75V
R40A, R40B | 311-16.0KHRDKR-ND | Resistor | Resistor | 2 | 0603-RES | Yageo | | | 16k | 1% | | 50V | 50V
R41A, R41B | 311-180KHRDKR-ND | Resistor | Resistor | 2 | 0603-RES | Yageo | | | 180k | 1% | | 50V | 50V
R42 | P1.00KHDKR-ND | Resistor | Resistor | 1 | 0603-RES | Panasonic | | | 1kR | 1% | | 75V | 75V
R49 | YAG3582DKR-ND | Resistor | Resistor | 1 | 0603-RES | Yageo | | | 240 | 1% | | 50V
R54, R55 | 311-330HRDKR-ND | Resistor | Resistor | 2 | 0603-RES | Yageo | | | 330R | 1% | | 50V | 50V
R56 | P5.1KDBDKR-ND | Resistor | Resistor | 1 | 0603-RES | Panasonic | | | 5.1kR | 0.1% | | 75V | 75V
SW1, SW3 | 450-1662-ND | 1825027-5 | SWITCH TACTILE SPST-NO 0.05A 24V | 2 | 1825027-5 | TE Connectivity | | | | | | | 24V
SW2 | CT1942MST-ND | 194-2MST | SWITCH PIANO DIP SPST 50MA 24V | 1 | 194-2MST

Designator | Supplier Part Number 1 | Comment | Description | Quantity | Footprint | Manufacturer | Capacitance | Colour | Resistance | Tolerance | Voltage | Voltage Rating | Voltage Rating (DC)
TP1A, TP1B, TP1C, TP1D, TP2A, TP2B, TP2C, TP2D, TP3A, TP3B, TP3C, TP3D, TP4A, TP4B, TP4C, TP4D, TP5A, TP5B, TP5C, TP5D, TP6A, TP6B, TP6C, TP6D, TP7A, TP7B, TP7C, TP7D, TP8A, TP8B, TP8C, TP8D, TP9A, TP9B, TP9C, TP9D, TP10A, TP10B, TP10C, TP10D, TP11A, TP11B, TP11C, TP11D, TP12A, TP12B, TP12C, TP12D, TP14, TP16, TP18, TP19, TP20, TP21, TP22, TP23, TP24, TP25, TP26, TP27, TP28, TP29, TP30, TP31, TP32, TP33, TP34, TP35, TP36, TP37, TP38, TP39, TP40, TP41, TP42, TP43 | A106145CT-ND | Test Point | Test Point | 76 | RCU-0C
U1, U2 | LTC2320CUKG-14#PBF-ND | LTC2320-14 | IC ADC 14BIT 1.5MSPS SAR 52QFN - 14 Bit Analog to Digital Converter 8 Input 4 SAR 52-QFN (7x8) | 2 | QFN52 | Analog Devices / Linear Technology
U3, U14 | 945-2987-ND | DCDC Converter RS6 | Recom RS6 | 2 | RS6 DCDC | Recom
U4, U13A, U13B, U13C, U13D, U13E, U13F | ADG3308BRUZ-ND | ADG3308 | IC XLATOR 8CH 1.2-5.5V 20TSSOP | 7 | TSSOP-20 | [NoParam], Analog Devices
U5 | MAX3098EACSE+-ND | MAX3097E | IC RS485/422 RX 32MBPS 16-QSOP | 1 | SOIC16_N
U6, U9 | 296-18593-6-ND | SN74LVC8T245PWR | IC BUS TRANSCVR 8BIT 24TSSOP | 2 | TSSOP24 | Texas Instruments
U7, U8, U10, U11 | 296-16845-6-ND | SN74LVC2T45DCTR | IC BUS TRANSCVR 2BIT N-INV SM8 | 4 | SM8 | Texas Instruments
U12A, U12B, U12C, U12D, U12E, U12F, U15A, U15B, U15C, U15D, U15E, U15F | TC4468COE-ND | TC4468 | IC MOSFET DVR QUAD AND 16SOIC | 12 | SOIC16_N - wide | Microchip
U16A, U16B, U16C, U16D, U16E, U16F, U16G, U16H, U16I, U16J, U16K, U16L, U16M, U16N, U16O, U16P | 296-16845-1-ND | SN74LVC2T45DCTR | IC BUS TRANSCVR 2BIT N-INV SM8 | 16 | SM8 | Texas Instruments
U17 | 555-1311-ND | DCDC Converter SHHD003A0A41Z | DC/DC CONVERTER 15W 5V 3A | 1 | DCDC SHHD003A0A41-SRZ | GE
U18 | LTC4365CTS8#TRMPBFCT-ND | LTC4365 | Overvoltage, Undervoltage and Reverse Supply Protection Controller | 1 | TS8 | Analog Devices / Linear Technology
U19A, U19B | REF3020AIDBZTDKR-ND | REF3020AIDBZT | Series Voltage Reference IC ±0.2% 25mA SOT-23-3 | 2 | SOT23-3
U20 | 296-34943-1-ND | TPS22965DSGT | IC LOAD SWITCH 6A 8WSON | 1 | 8-WFDFN Exposed Pad
U34 | 1727-4560-2-ND | 74LVC1T45GW,125 | TXRX XLATING DUAL 3ST 6TSSOP | 1 | SOT363-6N
U37A, U37B | LT1764EQ-1.8#PBF-ND | LT1764EQ-1.8#PBF-ND | IC REG LINEAR 1.8V 3A 5DDPAK | 2 | 5-DDPAK
U39 | LT1764EQ-3.3#PBF-ND | LT1764EQ-3.3#PBF | IC REG LINEAR 3.3V 3A 5DDPAK | 1 | 5-DDPAK | Analog Devices / Linear Technology
U40A, U40B | LT1529CQ-5#PBF-ND | LT1529CQ-5#PBF | IC REG LINEAR 5V 3A 5DDPAK | 2 | 5-DDPAK | Analog Devices / Linear Technology
U41A, U41B | ADP7118AUJZ-R7-ND | ADP7118AUJZ-R7 | IC REG LINEAR 200MA TSOT23-5 | 2 | TSOT-23 | Analog Devices
U42A, U42B | ADP7182AUJZ-R7-ND | ADP7182AUJZ-R7 | IC REG LINEAR 200MA 5TSOT | 2 | TSOT-23 | Analog Devices
U43 | 296-29537-1-ND | TPS2051C | IC USB PWR SW 1CH 0.5A SOT23-5 | 1 | SOT23-5 | Texas Instruments | | | | | 5.5V
U44 | 336-3692-ND | CP2102N | IC BRIDGE USB TO UART 20QFN | 1 | QFN20 | Silicon Labs
U46A, U46B, U46C, U46D | ADA4522-4ARUZ-RLCT-ND | ADA4522-4 | | 4 | TSSOP-14 | Analog Devices
U47A, U47B, U47C, U47D, U48A, U48B, U48C, U48D | INA2143UA-ND | INA2143UA | IC OPAMP DIFF 150KHZ 14SOIC | 8 | SOIC127P600X175-14N | Texas Instruments

591

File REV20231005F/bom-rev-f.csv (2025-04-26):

Quantity | Designator | Description | Value | Footprint | Supplier Part Number | Manufacturer Part Number | Manufacturer | Supplier
30 | C1, C2, C3, C4, C8, C13, C18, C22, C39, C44, C50, C51, C52, C53, C54, C55, C56, C61, C62, C63, C64, C83, C87, C89, C90, C96, C97, C104, C105, C106 | Capacitor | 10uF | 0603-CAP | 1276-1192-6-ND | CL10A106KP8NNNC | Samsung | DigiKey
34 | C5, C26, C43, C45, C57, C58, C59, C60, C72A, C72B, C72C, C72D, C72E, C72F, C75A, C75B, C75C, C75D, C75E, C75F, C82A, C82B, C84A, C84B, C85A, C85B, C88A, C88B, C91, C98, C103, C115, C116, C117 | Capacitor | 1uF | 0603-CAP | 1276-6524-6-ND | CL10B105MO8NNWC | Samsung | Digi-Key
85 | C6, C7, C9, C10, C11, C12, C14, C15, C16, C17, C19, C20, C21, C23, C24, C25, C27, C28, C29, C30, C31, C32, C33, C34, C65, C66, C67, C68, C69, C70, C71A, C71B, C71C, C71D, C71E, C71F, C73A, C73B, C73C, C73D, C73E, C73F, C74A, C74B, C74C, C74D, C74E, C74F, C76A, C76B, C76C, C76D, C76E, C76F, C92, C93A, C93B, C93C, C93D, C93E, C93F, C93G, C93H, C94A, C94B, C94C, C94D, C94E, C94F, C94G, C94H, C99, C100, C101, C102, C107, C110, C111, C112, C113, C114, C118A, C118B, C119A, C119B | Capacitor | 0.1uF | 0603-CAP | 1276-1012-6-ND | CL10F104ZB8NNNC | Samsung | DigiKey
6 | C35, C36, C41, C42, C47, C48 | Capacitor | 1000pF, 2kV | 1808-CAP | 709-1046-6-ND |  |  | Digi-Key
6 | C37, C38, C40, C46, C49, C95 | Capacitor | 6.8uF, 50V | 1812-CAP | 445-3919-6-ND | C4532X7R1H685K250KB | TDK | Digikey
10 | C77A, C77B, C79A, C79B, C81A, C81B, C86A, C86B, C108, C109 | Capacitor | 33nF | 0603-CAP | 1276-2041-1-ND | CL10B333KB8NNNC | Samsung | DigiKey
1 | C78 | Polarized Capacitor (Radial) | 1000uF | CAP - UVR1H102MHD1TO | 493-12786-1-ND | UVR1H102MHD1TO | Nichicon | Digikey
1 | C80 | Polarized Capacitor (Radial) | 100uF | CAP - UWT1V101MCL1GS | 493-2203-6-ND | UWT1V101MCL1GS | Nichicon | Digi-Key
1 | CON1 | CONN MOD JACK 8P8C R/A SHIELDED |  | RJSAE538004 | RJSAE538004-ND | RJSAE538004 | Amphenol Communications Solutions | Digikey
4 | CON2, CON3, CON4, CON5 |  |  | 1935161 | 277-1667-ND | PT1.5/2-5.0-H | Phoenix Contact | Digikey
1 | CON6 | CONN D-SUB RCPT 9POS R/A SLDR |  | L17H2220131 | L17H2220131-ND | L17H2220131 | Amphenol ICC / FCI | Digikey
1 | CON7 |  |  | L829-1J1T-43 | 380-1110-ND | L829-1J1T-43 | BEL MAGNETIC SOLUTIONS | Digi-Key
6 | CON9, CON10A, CON10B, CON10C, CON10D, CON11 | CONN D-SUB PLUG 15POS R/A SLDR |  | 178-H15-513R577 | NOR1831-ND | 178-H15-513R577 | NorComp | Digikey
1 | CON13 | CONN RCPT USB2.0 TYPEB 4POS R/A |  | UJ2-BH-4-TH | 102-5885-ND | UJ2-BH-4-TH | Same Sky | Digikey
3 | CON16, CON17, CON18 | CONN HEADER 100POS .8MM DUAL SMD |  |  | 609-1693-1-ND | 61083-102402LF | Amphenol ICC / FCI | Digikey
1 | HEATSINK1 | ALUM HEAT SINK FOR RASPBERRY PI |  |  | 1528-1697-ND | 3083 | Adafruit Industries | Digikey
10 | JMP1, JMP2, JMP3, JMP4, JMP5, JMP6, JMP7, JMP8, JMP9, JMP10 | CONN JUMPER SHORTING .100" GOLD |  |  | S9337-ND | QPC02SXGN-RC | Sullins | Digikey
7 | JP1, JP4, JP5, JP6, JP7, JP11, JP12 |  |  | PIN_HEADER_1X3 | 732-5316-ND | 61300311121 | Wurth Electronics | Digikey
5 | JP2, JP3, JP8, JP9, JP10 |  |  | PIN_HEADER_1x2 | 732-5315-ND | 61300211121 | Wurth Electronics | Digikey
1 | L1 | CMC 450UH 6.5A 2LN TH |  | CMC 744273801 | 732-2215-6-ND | 744273801 | Wurth Electronics | DigiKey
1 | L2 | FIXED IND 220UH 1.8A 300 MOHM | 220uH | 7447709221 | 732-1696-1-ND | 7447709221 | Wurth Electronics | Digikey
1 | LED1 |  | YELLOW | 0603-LED | 160-1448-6-ND | LTST-C191KSKT | Vishay Lite-On | Digikey
1 | LED2 |  | RED | 0603-LED | 160-1447-6-ND | LTSTC191KRKT | Vishay Lite-On | Digikey
1 | LED3 |  | GREEN | 0603-LED | 160-1446-6-ND | LTST-C191KGKT | Vishay Lite-On | Digikey
1 | M1 | JTAG-SMT3-NC: SURFACE-MOUNT PROG |  | JTAG-SMT3-NC | 1286-1196-ND | 410-357-B | Digilent | Digikey
1 | PICOZED1 | PicoZed 7030 SOM Evaluation Board with ARM Cortex-A9 1 x 10/100/1000 eMMC/QSPI Flash |  |  | AES-Z7PZ-7Z030-SOM-I-G/REV-E |  |  | Newark
2 | Q1, Q2 |  |  | SOT95P245X110-3N | FDV301NCT-ND | FDV301N | ON Semiconductor / Fairchild | Digi-Key
1 | Q3 | MOSFET N-CHAN DUAL 60V SO-8 |  | SOIC127P600X175-8N | SI4946CDY-T1-GE3DKR-ND | SI4946CDY-T1-GE3 | Vishay | Digikey
51 | R1, R9, R10, R17A, R17B, R17C, R17D, R18, R19, R20, R22, R23, R24, R25, R26, R27, R28, R29, R30, R31, R32, R33, R34, R35, R36, R37, R46, R57, R64, R65, R70, R71, R72, R73, R74, R75, R76, R77, R78, R79, R80, R81, R82, R95A, R95B, R95C, R95D, R96A, R96B, R96C, R96D | Resistor | 0R | 1206-RES | 311-0.0ERCT-ND | RC1206JR-070RL | Yageo | Digikey
5 | R2, R3, R4, R48, R49 | Resistor | 470 | 0603-RES | 311-470LDCT-ND | AC0603FR-07470RL | Yageo | Digi-Key
18 | R5, R6, R7, R11, R12, R13, R14, R15, R16, R21, R60A, R60B, R61A, R61B, R62A, R62B, R63A, R63B | Resistor | 100 | 0603-RES | YAG3561DKR-ND | AC0603FR-07100RL | Yageo | Digikey
10 | R8, R38, R39, R40, R41, R42, R43, R44, R45, R99 | Resistor | 10k | 0603-RES | P10.0KHCT-ND | ERJ-3EKF1002V | Panasonic | Digikey
9 | R47, R93A, R93B, R93C, R93D, R94A, R94B, R94C, R94D | Resistor | DNP | 1206-RES | 311-0.0ERCT-ND | RC1206JR-070RL | Yageo | Digikey
1 | R55 | Resistor | 390k | 0603-RES | 311-390KHRCT-ND | RC0603FR-07390KL | Yageo | Digikey
1 | R56 | Resistor | 178k | 0603-RES | 311-178KHRCT-ND |  |  | Digi-Key
1 | R58 | Resistor | 4k12 | 0603-RES | 311-4.12KHRCT-ND | RC0603FR-074K12L | Yageo | Digikey
1 | R59 | Resistor | 5k9 | 0603-RES | 311-5.90KHRCT-ND | RC0603FR-075K9L | Yageo | Digikey
10 | R83, R84, R85, R86, R87, R88, R89, R90, R91, R92 | Resistor | 100k | 0603-RES | 311-100KLDCT-ND | AC0603FR-07100KL | Yageo | Digikey
1 | R98 | Resistor | 4k7 | 0603-RES | 311-4.70KHRCT-ND | RC0603FR-074K7L | Yageo | Digikey
48 | RT1A, RT1B, RT1C, RT1D, RT2A, RT2B, RT2C, RT2D, RT3A, RT3B, RT3C, RT3D, RT4A, RT4B, RT4C, RT4D, RT5A, RT5B, RT5C, RT5D, RT6A, RT6B, RT6C, RT6D, RT7A, RT7B, RT7C, RT7D, RT8A, RT8B, RT8C, RT8D, RT9A, RT9B, RT9C, RT9D, RT10A, RT10B, RT10C, RT10D, RT11A, RT11B, RT11C, RT11D, RT12A, RT12B, RT12C, RT12D | PTC RESET FUSE 24V 40MA 0603 |  | PTCC1607X06N | 507-0ZCM0004FF2GCT-ND |  |  | Digi-Key
13 | SCREW1, SCREW2, SCREW3, SCREW4, SCREW5, SCREW6, SCREW7, SCREW8, SCREW9, SCREW10, SCREW11, SCREW12, SCREW13 |  |  |  | 36-9900-ND | 9900 | Keystone Electronics | Digikey
13 | STANDOFF1, STANDOFF2, STANDOFF3, STANDOFF4, STANDOFF5, STANDOFF6, STANDOFF7, STANDOFF8, STANDOFF9, STANDOFF10, STANDOFF11, STANDOFF12, STANDOFF13 |  |  |  | 36-1656-ND | 1656 | Keystone Electronics | Digikey
1 | SW1 | SWITCH TACTILE SPST-NO 0.05A 24V |  | 1825027-5 | 450-1662-ND | 1825027-5 | TE Connectivity | Digikey
4 | TP1, TP2, TP3, TP4 | Test Point |  | RCU-0C | A106145CT-ND | 1625854-3 | TE Connectivity | Digikey
1 | U1 | IC ADC 14BIT 1.5MSPS SAR 52QFN - 14 Bit Analog to Digital Converter 8 Input 4 SAR 52-QFN (7x8) |  | QFN50P700X800X80_HS-53N | LTC2320CUKG-14#PBF-ND | LTC2320CUKG-14#PBF | Analog Devices / Linear Technology | Digikey
1 | U2 | Series Voltage Reference IC ±0.2% 25mA SOT-23-3 |  | SOT23-3 | REF3020AIDBZTDKR-ND | REF3020AIDBZT | Texas Instruments | Digikey
4 | U3, U12, U42, U44 | TXRX XLATING DUAL 3ST 6TSSOP |  | SOT65P210X110-6N | 1727-4560-1-ND | 74LVC1T45GW,125 | Nexperia USA | Digi-Key
5 | U4, U6, U22, U34, U47 | IC RCVR RS422 QUAD DIFF 16TSSOP |  | TSOP65P640X120-16N | 296-30088-1-ND | AM26C32IPWR | Texas Instruments | Digikey
15 | U5, U24A, U24B, U24C, U24D, U24E, U24F, U31A, U31B, U31C, U31D, U31E, U31F, U31G, U31H | IC BUS TRANSCVR 8BIT 24TSSOP |  | TSOP65P640X120-24N | 296-18593-1-ND | SN74LVC8T245PWR | Texas Instruments | Digikey
1 | U7 | DC-DC ISOLATED, 6 W, 9~36 VDC IN |  | PQQ6W-Q24-S24-S | 102-PQQ6W-Q24-S24-S-ND | PQQ6W-Q24-S24-S | CUI | Digi-Key
3 | U8, U32, U45 | TVS DIODE 5.5V 10V 6TSOP |  | TSOP95P280X110-6N | NUP4114HMR6T1GOSCT-ND | NUP4114HMR6T1G | ON Semiconductor | Digikey
3 | U9, U49, U50 | Res Thick Film Array 120 Ohm 5% ±200ppm/C ISOL 8-Pin 1206(4 X 0603) Convex SMD Automotive T/R | 120R | EXB-38V121JV | Y9121CT-ND | EXB-38V121JV | Panasonic | Digikey
4 | U10, U39, U40, U41 | LED RGB 5050 SMD |  | IN-PI556FCH | 1830-1107-1-ND | IN-PI556FCH | Inolux | Digikey
2 | U11, U13 | Recom RS6 |  | RS6 DCDC | 945-2987-ND | RS6-2415S | Recom | Digikey
1 | U14 | DC DC CONVERTER 5V 15W |  | DCDC SHHD003A0A41-SRZ | 555-1312-ND | SHHD003A0A4Z | OmniOn Power | DigiKey
2 | U15, U20 | IC REG LINEAR 5V 3A 5DDPAK |  | 5-DDPAK | LT1529CQ-5#PBF-ND |  |  | Digi-Key
1 | U16 | IC REG LINEAR 1.8V 600MA SOT25 |  | SOT95P280X145-5N | AP2112K-1.8TRG1DICT-ND | AP2112K-1.8TRG1 | Diodes | Digikey
1 | U17 | IC REG LINEAR 3.3V 1A SOT223 |  | SOT230P700X180-4N | AP2114H-3.3TRG1DICT-ND | AP2114H-3.3TRG1 | Diodes | Digikey
1 | U18 | IC REG LINEAR 15V 500MA DPAK |  | DPAK229P991X238-3N | MC78M15CDTRKGOSCT-ND | MC78M15CDTRKG | ON Semiconductor | Digikey
1 | U19 | IC REG LINEAR -15V 500MA DPAK |  | DPAK229P991X238-3N | MC79M15CDTRKGOSCT-ND | MC79M15CDTRKG | ON Semiconductor | Digikey
1 | U21 | IC REG LINEAR 1.8V 3A 5DDPAK |  | 5-DDPAK | LT1764EQ-1.8#PBF-ND | LT1764EQ-1.8#PBF | Analog Devices / Linear Technology | Digikey
12 | U23A, U23B, U23C, U23D, U23E, U23F, U25A, U25B, U25C, U25D, U25E, U25F | IC MOSFET DVR QUAD AND 16SOIC |  | SOIC16_N - wide | TC4468COE-ND | TC4468COE | Microchip | Digikey
1 | U26 | IC OVERVOLTAGE PROT TSOT23-8 |  | TSOP65P280X100-8N | LTC4365CTS8#TRMPBFCT-ND |  |  | Digi-Key
1 | U27 | IC EEPROM 128K SPI 20MHZ 8SOIC |  | SOIC127P600X175-8N | CAT25128VI-GT3OSCT-ND | CAT25128VI-GT3 | ON Semiconductor | Digikey
4 | U28A, U28B, U29A, U29B | IC OPAMP DIFF 150KHZ 14SOIC |  | SOIC127P600X175-14N | INA2143UA-ND | INA2143UA | Texas Instruments | Digikey
1 | U30 | IC LOAD SWITCH 6A 8WSON |  | SON50P200X80_HS-9N | 296-34943-1-ND | TPS22965DSGT | Texas Instruments | DigiKey
3 | U33, U46, U48 | IC DRIVER 4/0 16TSSOP |  | TSOP65P640X120-16N | 296-30087-1-ND | AM26C31IPWR | Texas Instruments | Digikey
4 | U35, U36, U37, U38 | TVS DIODE 12V 19V 8SO |  | SOIC127P600X175-8N | 1655-1701-1-ND |  |  | Digi-Key
1 | U43 | IC GATE AND 1CH 2-INP SOT353 |  | SOT65P210X110-5N | 74AHCT1G08SE-7DICT-ND | 74AHCT1G08SE-7 | Diodes | Digikey

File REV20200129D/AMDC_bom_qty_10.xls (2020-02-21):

Quantity | Supplier Part Number 1 | Designator | Comment | Value | Supplier Order Qty 1
2 | 1727-4560-1-ND | U3, U12 | 74LVC1T45GW,125 |  | 20
5 | NOR1832-ND | CON8, CON10A, CON10B, CON10C, CON10D | 178-H15-513R497 |  | 50
1 | 450-1662-ND | SW1 | 1825027-5 |  | 10
2 | A97799TR-ND | CON9, CON12 | 1981584-1
1 | 732-1696-1-ND | L2 | 7447709221 | 220uH | 10
1 | 296-30087-1-ND | U8 | AM26C31 |  | 10
3 | 296-30088-1-ND | U4, U6, U7 | AM26C32 |  | 30
1 | AP2112K-1.8TRG1DICT-ND | U16 | AP2112K-1.8TRG1 |  | 10
1 | AP2114H-3.3TRG1DICT-ND | U17 | AP2114H-3.3TRG1 |  | 10
1 | 493-2203-6-ND | C80 | Cap Pol1 | 100uF | 10
1 | 493-12786-1-ND | C78 | Cap Pol1 | 1000uF | 10
3 | 445-9015-6-ND | C39, C44, C50 | Capacitor | 10uF | 30
5 | 445-3919-6-ND | C37, C38, C40, C46, C49 | Capacitor | 6.8uF, 50V | 50
6 | 709-1046-6-ND | C35, C36, C41, C42, C47, C48 | Capacitor | 1000pF, 2kV | 60
8 | 478-1548-6-ND | C77A, C77B, C79A, C79B, C81A, C81B, C86A, C86B | Capacitor | 33nF | 80
11 | 1276-1192-6-ND | C1, C51, C52, C53, C54, C55, C56, C61, C62, C63, C64 | Capacitor | 10uF | 110
14 | 1276-1119-6-ND | C2, C3, C4, C8, C13, C18, C22, C83, C87, C89, C90, C104, C105, C106 | Capacitor | 10uF | 140
34 | 1276-6524-6-ND | C5, C26, C43, C45, C57, C58, C59, C60, C66, C67, C69, C70, C72A, C72B, C72C, C72D, C72E, C72F, C75A, C75B, C75C, C75D, C75E, C75F, C82A, C82B, C84A, C84B, C85A, C85B, C88A, C88B, C91, C103 | Capacitor | 1uF | 340
35 | 1276-1012-6-ND | C24, C25, C27, C28, C29, C30, C71A, C71B, C71C, C71D, C71E, C71F, C73A, C73B, C73C, C73D, C73E, C73F, C74A, C74B, C74C, C74D, C74E, C74F, C76A, C76B, C76C, C76D, C76E, C76F, C99, C100, C101, C102, C107 | Capacitor | 100nF | 350
43 | 1276-1012-6-ND | C6, C7, C9, C10, C11, C12, C14, C15, C16, C17, C19, C20, C21, C23, C31, C32, C33, C34, C65, C68, C92, C93A, C93B, C93C, C93D, C93E, C93F, C94A, C94B, C94C, C94D, C94E, C94F, C95, C96, C97A, C97B, C97C, C97D, C98A, C98B, C98C, C98D | Capacitor | 0.1uF | 430
1 | CAT25128VI-GT3OSCT-ND | U27 | CAT25128VI-GT3 |  | 10
1 | 732-2215-6-ND | L1 | CMC 744273801 |  | 10
1 | 336-5888-1-ND | U22 | CP2102N |  | 10
2 | 945-2987-ND | U11, U13 | DCDC Converter RS6 |  | 20
2 | 553-1536-1-ND | T1, T2 | HX1188NLT |  | 20
4 | INA2143UA-ND | U28A, U28B, U29A, U29B | INA2143UA |  | 40
4 | 1830-1107-1-ND | U10, U39, U40, U41 | IN-PI556FCH |  | 40
1 | 1286-1192-ND | CON11 | JTAG-SMT2-NC |  | 10
5 | 732-5315-ND | JP2, JP3, JP8, JP9, JP10 | Jumper2 |  | 50
5 | 732-5316-ND | JP1, JP4, JP5, JP6, JP7 | Jumper3 |  | 50
1 | L17H2220131-ND | CON6 | L17H2220131 |  | 10
1 | 380-1110-ND | CON7 | L829-1J1T-43 |  | 10
2 | 160-1446-6-ND | LED3, LED13 | LED | GREEN | 20
2 | 160-1447-6-ND | LED2, LED12 | LED | RED | 20
2 | 160-1448-6-ND | LED1, LED14 | LED | YELLOW | 20
2 | LT1529CQ-5#PBF-ND | U15, U20 | LT1529CQ-5#PBF |  | 20
1 | LT1764EQ-1.8#PBF-ND | U21 | LT1764EQ-1.8#PBF-ND |  | 10
1 | LTC2320CUKG-14#PBF-ND | U1 | LTC2320-14 |  | 10
1 | LTC4365CTS8#TRMPBFCT-ND | U26 | LTC4365 |  | 10
4 | LTC6820IMS#TRPBFCT-ND | U9A, U9B, U9C, U9D | LTC6820IMS#TRPBF |  | 40
1 | MC78M15CDTRKGOSCT-ND | U18 | MC78M15CDTRKG |  | 10
1 | MC79M15CDTRKGOSCT-ND | U19 | MC79M15CDTRKG |  | 10
2 | FDV301NCT-ND | Q1, Q2 | MOSFET |  | 20
3 | NUP4114HMR6T1GOSCT-ND | U32, U33, U34 | NUP4114HMR6T1G |  | 30
1 | REF3020AIDBZTDKR-ND | U2 | REF3020AIDBZT |  | 10
1 | 311-0.0ERCT-ND | R47 | Resistor | DNP | 10
1 | 311-121KHRCT-ND | R58 | Resistor | 121k | 10
2 | 311-178KHRCT-ND | R56, R59 | Resistor | 178k | 20
2 | 541-5.90MHCT-ND | R55, R83 | Resistor | 5.9M | 20
4 | 311-1.20KHRCT-ND | R19A, R19B, R19C, R19D | Resistor | 1.2k | 40
4 | 311-120HRCT-ND | R66, R67, R68, R69 | Resistor | 120 | 40
6 | 311-470LDCT-ND | R2, R3, R4, R49, R51, R52 | Resistor | 470 | 60
8 | 311-2.80KHRCT-ND | R9A, R9B, R9C, R9D, R10A, R10B, R10C, R10D | Resistor | 2.8k | 80
8 | 311-100KLDCT-ND | R84, R85, R86, R87, R88, R89, R90, R91 | Resistor | 100k | 80
10 | P0.0GDKR-ND | R1, R17, R18, R20, R21A, R21B, R21C, R21D, R38, R50 | Resistor | DNP | 100
10 | P10.0KHCT-ND | R8, R39, R40, R41, R42, R43, R44, R45, R53, R54 | Resistor | 10k | 100
18 | YAG3561DKR-ND | R5, R6, R7, R11, R12, R13, R14, R15, R16, R48, R60A, R60B, R61A, R61B, R62A, R62B, R63A, R63B | Resistor | 100 | 180
33 | 311-0.0ERCT-ND | R22, R23, R24, R25, R26, R27, R28, R29, R30, R31, R32, R33, R34, R35, R36, R37, R46, R57, R64, R65, R70, R71, R72, R73, R74, R75, R76, R77, R78, R79, R80, R81, R82 | Resistor | 0 | 330
1 | RJSAE538004-ND | CON1 | RJSAE538004 |  | 10
4 | 277-1667-ND | CON2, CON3, CON4, CON5 | ScrewTerminal_1x2 |  | 40
1 | 555-1312-ND | U14 | SHHD003A0A4Z |  | 10
1 | SI4946CDY-T1-GE3DKR-ND | Q3 | Si4946CDY |  | 10
4 | 1655-1701-1-ND | U35, U36, U37, U38 | SMDA12CTR |  | 40
7 | 296-18593-1-ND | U5, U24A, U24B, U24C, U24D, U24E, U24F | SN74LVC8T245 |  | 70
6 | 296-18593-6-ND | U31A, U31B, U31C, U31D, U31E, U31F | SN74LVC8T245PWR |  | 60
12 | TC4468COE-ND | U23A, U23B, U23C, U23D, U23E, U23F, U25A, U25B, U25C, U25D, U25E, U25F | TC4468 |  | 120
4 | A106145CT-ND | TP1, TP2, TP3, TP4 | Test Point |  | 40
1 | 296-34943-1-ND | U30 | TPS22965DSGT |  | 10

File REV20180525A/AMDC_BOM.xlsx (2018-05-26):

Supplier Part Number 1 | Manufacturer Part Number 1 | Manufacturer 1 | Comment | Designator | Quantity | Value | Footprint
TC4468COE-ND (https://octopart-clicks.com/click/altium?sku=TC4468COE-ND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) | TC4468COE (https://octopart-clicks.com/click/altium?sku=TC4468COE-ND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) | Microchip (https://octopart-clicks.com/click/altium?sku=TC4468COE-ND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) | TC4468 | U12A, U12B, U12C, U12D, U12E, U12F, U15A, U15B, U15C, U15D, U15E, U15F | 12 |  | SOIC16_N
RP40-2415DGW-ND (https://octopart-clicks.com/click/altium?sku=RP40-2415DGW-ND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) | RP40-2415DGW (https://octopart-clicks.com/click/altium?sku=RP40-2415DGW-ND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) | Recom (https://octopart-clicks.com/click/altium?sku=RP40-2415DGW-ND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) | RP40-2415DG | U35 | 1 |  | RP40-G
RB521S30T1GOSTR-ND (https://octopart-clicks.com/click/altium?sku=RB521S30T1GOSTR-ND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) | RB521S30T1G (https://octopart-clicks.com/click/altium?sku=RB521S30T1GOSTR-ND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) | ON Semiconductor (https://octopart-clicks.com/click/altium?sku=RB521S30T1GOSTR-ND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) | RB521 | D2 | 1 |  | SOD-523
MAX3097ECEE+-ND (https://octopart-clicks.com/click/altium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) | MAX3097ECEE+ (https://octopart-clicks.com/click/altium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) | Maxim (https://octopart-clicks.com/click/altium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) | MAX3097E | U5 | 1 |  | SOP127P826-16L
LTC2320CUKG-14#PBF-ND (https://octopart-clicks.com/click/altium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) | LTC2320CUKG-14#PBF (https://octopart-clicks.com/click/altium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) | Analog Devices / Linear Technology (https://octopart-clicks.com/click/altium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) | LTC2320-14 | U1, U2 | 2 |  | QFN52
LT1764EQ-3.3#PBF-ND (https://octopart-clicks.com/click/altium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) | LT1764EQ-3.3#PBF (https://octopart-clicks.com/click/altium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) | Analog Devices / Linear Technology (https://octopart-clicks.com/click/altium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) | LT1764EQ-3.3#PBF | U39 | 1 |  | 5-DDPAK
LT1764EQ-1.8#PBF-ND (https://octopart-clicks.com/click/altium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) | LT1764EQ-1.8#PBF (https://octopart-clicks.com/click/altium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) | Analog Devices / Linear Technology (https://octopart-clicks.com/click/altium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) | LT1764EQ-1.8#PBF-ND | U37A, U37B | 2 |  | 5-DDPAK
LT1529CQ-5#PBF-ND (https://octopart-clicks.com/click/altium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) | LT1529CQ-5#PBF (https://octopart-clicks.com/click/altium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) | Analog Devices / Linear Technology (https://octopart-clicks.com/click/altium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) | LT1529CQ-5#PBF | U40A, U40B | 2 |  | 5-DDPAK
LT1461CCS8-2.5#PBF-ND (https://octopart-clicks.com/click/altium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) | LT1461CCS8-2.5#PBF (https://octopart-clicks.com/click/altium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) | Analog Devices / Linear Technology (https://octopart-clicks.com/click/altium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) | LT1461CCS8-2.5#PBF | U45 | 1 |  | SOIC8_N
INA2143UA-ND (https://octopart-clicks.com/click/altium?sku=INA2143UA-ND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) | INA2143UA (https://octopart-clicks.com/click/altium?sku=INA2143UA-ND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) | Texas Instruments (https://octopart-clicks.com/click/altium?sku=INA2143UA-ND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) | INA2143UA | U47A, U47B, U48A, U48B | 4 |  | SOIC14_N
F2895TR-ND (https://octopart-clicks.com/click/altium?sku=F2895TR-ND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) | SP1001-04JTG (https://octopart-clicks.com/click/altium?sku=F2895TR-ND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) | Littelfuse (https://octopart-clicks.com/click/altium?sku=F2895TR-ND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) | SP1001-04JTG | D1, D3, D7, D8 | 4 |  | SC70-5
DMN65D8L-7DITR-ND (https://octopart-clicks.com/click/altium?sku=DMN65D8L-7DITR-ND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) | DMN65D8L-7 (https://octopart-clicks.com/click/altium?sku=DMN65D8L-7DITR-ND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) | Diodes (https://octopart-clicks.com/click/altium?sku=DMN65D8L-7DITR-ND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) | MOSFET | Q1, Q2, Q3, Q4, Q5, Q6, Q7, Q8 | 8 |  | SOT95P250-3N
CT1943MST-ND (https://octopart-clicks.com/click/altium?sku=CT1943MST-ND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) | 194-3MST (https://octopart-clicks.com/click/altium?sku=CT1943MST-ND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) | CTS (https://octopart-clicks.com/click/altium?sku=CT1943MST-ND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) | 194-3MST | SW2 | 1 |  | 194-3MST
AE10921-ND (https://octopart-clicks.com/click/altium?sku=AE10921-ND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) | A-DF09A/KG-T2S (https://octopart-clicks.com/click/altium?sku=AE10921-ND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) | Assmann (https://octopart-clicks.com/click/altium?sku=AE10921-ND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) | A-DF 09 A/KG-T2S | CON5 | 1 |  | A-DF 09 A/KG-T2S
ADP7182AUJZ-R7-ND (https://octopart-clicks.com/click/altium?sku=ADP7182AUJZ-R7-ND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) | ADP7182AUJZ-R7 (https://octopart-clicks.com/click/altium?sku=ADP7182AUJZ-R7-ND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) | Analog Devices (https://octopart-clicks.com/click/altium?sku=ADP7182AUJZ-R7-ND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) | ADP7182AUJZ-R7 | U42A, U42B, U42C, U42D | 4 |  | TSOT-23
ADP7118AUJZ-R7-ND (https://octopart-clicks.com/click/altium?sku=ADP7118AUJZ-R7-ND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) | ADP7118AUJZ-R7 (https://octopart-clicks.com/click/altium?sku=ADP7118AUJZ-R7-ND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) | Analog Devices (https://octopart-clicks.com/click/altium?sku=ADP7118AUJZ-R7-ND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) | ADP7118AUJZ-R7 | U41A, U41B, U41C, U41D | 4 |  | TSOT-23
ADG3308BRUZ-ND (https://octopart-clicks.com/click/altium?sku=ADG3308BRUZ-ND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) | ADG3308BRUZ (https://octopart-clicks.com/click/altium?sku=ADG3308BRUZ-ND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) | Analog Devices (https://octopart-clicks.com/click/altium?sku=ADG3308BRUZ-ND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) | ADG3308 | U4, U13A, U13B, U13C, U13D, U13E, U13F | 7 |  | TSSOP50P640-20N
ADA4522-4ARZ-ND (https://octopart-clicks.com/click/altium?sku=ADA4522-4ARZ-ND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) | ADA4522-4ARZ (https://octopart-clicks.com/click/altium?sku=ADA4522-4ARZ-ND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) | Analog Devices (https://octopart-clicks.com/click/altium?sku=ADA4522-4ARZ-ND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) | ADA4522-4 | U3A, U3B, U3C, U3D, U3E, U3F, U3G, U3H, U46A, U46B | 10 |  | TSSOP14
A115463-ND (https://octopart-clicks.com/click/altium?sku=A115463-ND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) | 5569257-1 (https://octopart-clicks.com/click/altium?sku=A115463-ND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) | TE Connectivity (https://octopart-clicks.com/click/altium?sku=A115463-ND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) | 5569257-1 | CON1 | 1 |  | 5569257-1
A97799TR-ND (https://octopart-clicks.com/click/altium?sku=A97799TR-ND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) | 1981584-1 (https://octopart-clicks.com/click/altium?sku=A97799TR-ND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) | TE Connectivity (https://octopart-clicks.com/click/altium?sku=A97799TR-ND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) | 1981584-1 | CON11, CON12 | 2 |  | 1981584-1
1727-4560-2-ND (https://octopart-clicks.com/click/altium?sku=1727-4560-2-ND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) | 74LVC1T45GW,125 (https://octopart-clicks.com/click/altium?sku=1727-4560-2-ND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) | Nexperia (https://octopart-clicks.com/click/altium?sku=1727-4560-2-ND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) | 74LVC1T45GW,125 | U34 | 1 |  | SOT363-6N
1115FFE-ND (https://octopart-clicks.com/click/altium?sku=1115FFE-ND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) | 178-015-513R571 (https://octopart-clicks.com/click/altium?sku=1115FFE-ND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) | NorComp (https://octopart-clicks.com/click/altium?sku=1115FFE-ND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) | 178-015-513R571 | CON7, CON8A, CON8B, CON8C, CON8D | 5 |  | 178-015-513R571
945-2397-5-ND (https://octopart-clicks.com/click/altium?sku=945-2397-5-ND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) | RP40-2405SG (https://octopart-clicks.com/click/altium?sku=945-2397-5-ND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) | Recom (https://octopart-clicks.com/click/altium?sku=945-2397-5-ND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) | RP40-2405SG | U36 | 1 |  | RP40-G
732-3883-ND (https://octopart-clicks.com/click/altium?sku=732-3883-ND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) | 7448227005 (https://octopart-clicks.com/click/altium?sku=732-3883-ND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) | Wurth Electronics (https://octopart-clicks.com/click/altium?sku=732-3883-ND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) | 7448227005 | L1, L2 | 2 |  | 7448227005
492-1243-2-ND (https://octopart-clicks.com/click/altium?sku=492-1243-2-ND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) | SM1210RGB (https://octopart-clicks.com/click/altium?sku=492-1243-2-ND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) | Bivar (https://octopart-clicks.com/click/altium?sku=492-1243-2-ND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) | LED_RGB_CA | LED4 | 1 |  | 1210-LED-RGB-CA
450-1662-ND (https://octopart-clicks.com/click/altium?sku=450-1662-ND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) | 1825027-5 (https://octopart-clicks.com/click/altium?sku=450-1662-ND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) | TE Connectivity (https://octopart-clicks.com/click/altium?sku=450-1662-ND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) | 1825027-5 | SW1, SW3 | 2 |  | 1825027-5
380-1110-ND (https://octopart-clicks.com/click/altium?sku=380-1110-ND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) | L829-1J1T-43 (https://octopart-clicks.com/click/altium?sku=380-1110-ND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) | Bel (https://octopart-clicks.com/click/altium?sku=380-1110-ND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) | L829-1J1T-43 | CON6 | 1 |  | L829-1J1T-43
336-3692-ND (https://octopart-clicks.com/click/altium?sku=336-3692-ND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) | CP2102N-A01-GQFN20 (https://octopart-clicks.com/click/altium?sku=336-3692-ND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) | Silicon Labs (https://octopart-clicks.com/click/altium?sku=336-3692-ND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) | CP2102N | U44 | 1 |  | QFN50P400X400-20V1L
296-40356-2-ND (https://octopart-clicks.com/click/altium?manufacturer=Texas%20Instruments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) | LP5907MFX-2.5/NOPB (https://octopart-clicks.com/click/altium?manufacturer=Texas%20Instruments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) | Texas Instruments (https://octopart-clicks.com/click/altium?manufacturer=Texas%20Instruments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) | LP5907MFX-2.5/NOPB | U38A, U38B, U38C, U38D | 4 |  | SOT23-5
296-29537-1-ND (https://octopart-clicks.com/click/altium?sku=296-29537-1-ND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) | TPS2051CDBVR (https://octopart-clicks.com/click/altium?sku=296-29537-1-ND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) | Texas Instruments (https://octopart-clicks.com/click/altium?sku=296-29537-1-ND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) | TPS2051C | U43 | 1 |  | SOT23-5
296-18593-2-ND (https://octopart-clicks.com/click/altium?sku=296-18593-2-ND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) | SN74LVC8T245PWR (https://octopart-clicks.com/click/altium?sku=296-18593-2-ND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) | Texas Instruments (https://octopart-clicks.com/click/altium?sku=296-18593-2-ND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) | SN74LVC8T245PWR | U6, U9 | 2 |  | TSSOP24
296-16845-2-ND (https://octopart-clicks.com/click/altium?sku=296-16845-2-ND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) | SN74LVC2T45DCTR (https://octopart-clicks.com/click/altium?sku=296-16845-2-ND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) | Texas Instruments (https://octopart-clicks.com/click/altium?sku=296-16845-2-ND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) | SN74LVC2T45DCTR | U7, U8, U10, U11, U16A, U16B, U16C, U16D, U16E, U16F, U16G, U16H, U16I, U16J, U16K, U16L, U16M, U16N, U16O, U16P | 20 |  | SM8
277-1667-ND (https://octopart-clicks.com/click/altium?sku=277-1667-ND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) | 1935161 (https://octopart-clicks.com/click/altium?sku=277-1667-ND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) | Phoenix Contact (https://octopart-clicks.com/click/altium?sku=277-1667-ND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) | ScrewTerminal_1x2 | CON2, CON3, CON4 | 3 |  | 1935161
 |  |  | Capacitor | C1, C6, C11, C15, C24, C31, C37, C43 | 8 | 100pF | 0603-CAP
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

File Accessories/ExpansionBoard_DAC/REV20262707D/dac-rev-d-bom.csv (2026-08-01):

Quantity | Designator | Description | Value | Footprint | Supplier Part Number | Manufacturer Part Number | Supplier | Manufacturer
9 | C1, C2, C3, C4, C21, C22, C23, C24, C42 | 0.1µF ±10% 25V Ceramic Capacitor X7R 0603 (1608 Metric) | 0.1uF | 0603-CAP | 311-1341-1-ND | CC0603KRX7R8BB104 | DigiKey | Yageo Group
12 | C5, C7, C9, C11, C13, C15, C17, C19, C37, C38, C39, C40 | 0.18µF ±10% 16V Ceramic Capacitor X7R 0603 (1608 Metric) | 0.18uF | 0603-CAP | 311-4066-1-ND | CC0603KRX7R7BB184 | DigiKey | Yageo Group
8 | C6, C8, C10, C12, C14, C16, C18, C20 | 10000pF ±10% 50V Ceramic Capacitor X7R 0603 (1608 Metric) | 10nF | 0603-CAP | 311-1085-1-ND | CC0603KRX7R9BB103 | DigiKey | Yageo Group
3 | C25, C32, C36 | 4.7µF ±10% 25V Ceramic Capacitor X5R 0603 (1608 Metric) | 4.7uF | 0603-CAP | 1276-1900-1-ND | CL10A475KA8NQNC | DigiKey | Samsung Electro-Mechanics
2 | C26, C29 | 0.47µF ±10% 16V Ceramic Capacitor X7R 0603 (1608 Metric) | 0.47uF | 0603-CAP | 1276-1062-1-ND | CL10B474KO8NNNC | DigiKey | Samsung Electro-Mechanics
8 | C27, C28, C30, C31, C33, C34, C35, C41 | 1µF ±10% 10V Ceramic Capacitor X5R 0603 (1608 Metric) | 1uF | 0603-CAP | 1276-1182-1-ND | CL10A105KP8NNNC | DigiKey | Samsung Electro-Mechanics
1 | CON1 | 15 Position D-Sub, High Density Receptacle, Female Sockets Connector |  | ICD15S13E6GX00LF | 609-2801-ND | ICD15S13E6GX00LF | DigiKey | Amphenol Communications Solutions
2 | CON2, CON3 | 6 Position Wire to Board Terminal Block Horizontal with Board 0.197" (5.00mm) Through Hole |  | 1935200 | 277-1581-ND | 1935200 | DigiKey | Phoenix Contact
8 | J1, J2, J3, J4, J5, J6, J7, J8 | CONN BNC JACK STR 75 OHM PCB |  | 0731711900 | WM5517-ND | 73171-1900 | DigiKey | Molex
8 | JMP1, JMP2, JMP3, JMP4, JMP5, JMP6, JMP7, JMP8 | CONN JUMPER SHORTING .100" GOLD |  |  | S9337-ND | QPC02SXGN-RC | DigiKey | Sullins
8 | JP1, JP2, JP3, JP4, JP5, JP6, JP7, JP8 | Connector Header Through Hole 3 position 0.100" (2.54mm) |  | PIN_HEADER_1X3 | SAM8995-ND | TSW-103-07-F-S | DigiKey | Samtec
12 | R6, R8, R14, R16, R22, R24, R30, R32, R38, R39, R40, R41 | 10 kOhms ±0.1% 0.2W, 1/5W Chip Resistor 0603 (1608 Metric) Automotive AEC-Q200, Pulse Withstanding Thick Film | 10K | 0603-RES | P20086CT-ND | ERJ-PB3B1002V | DigiKey | Panasonic
8 | R7, R9, R15, R17, R23, R25, R31, R33 | 120 Ohms ±1% 0.1W, 1/10W Chip Resistor 0603 (1608 Metric) Moisture Resistant Thick Film | 120 | 0603-RES | 311-120HRCT-ND | RC0603FR-07120RL | DigiKey | Yageo Group
8 | R10, R12, R18, R20, R26, R28, R34, R36 | 7.5 kOhms ±0.1% 0.2W, 1/5W Chip Resistor 0603 (1608 Metric) Automotive AEC-Q200, Pulse Withstanding Thick Film | 7.5K | 0603-RES | P20072CT-ND | ERJ-PB3B7501V | DigiKey | Panasonic
8 | R11, R13, R19, R21, R27, R29, R35, R37 | 30 kOhms ±0.1% 0.2W, 1/5W Chip Resistor 0603 (1608 Metric) Automotive AEC-Q200, Pulse Withstanding Thick Film | 30K | 0603-RES | P20138CT-ND | ERJ-PB3B3002V | DigiKey | Panasonic
1 | S1 | Tactile Switch SPST-NO Top Actuated Surface Mount |  | PTS647SK38SMTR2LFSCT-ND | PTS647SK38SMTR2LFSCT-ND | PTS647SK38SMTR2 LFS | Digi-Key | C&K
1 | S2 | SWITCH SLIDE DIP SPST 25MA 24V |  | SDA06H0SBR | CKN9495CT-ND | SDA06H0SBR | DigiKey | C&K Components
4 | SCREW1, SCREW2, SCREW3, SCREW4 | #4-40 Pan Head Machine Screw Phillips Drive Stainless Steel |  |  | 36-9900-ND | 9900 | DigiKey | Keystone
4 | STANDOFF1, STANDOFF2, STANDOFF3, STANDOFF4 | Hex Standoff Threaded #4-40 Aluminum 0.500" (12.70mm) 1/2" |  |  | 1772-1993-ND | 2057-440-AL-7 | DigiKey | RAF Hardware
5 | TP1, TP2, TP3, TP4, TP5 | Test Point |  | RCU-0C | A106145CT-ND | 1625854-3 | DigiKey | TE Connectivity
2 | U1, U2 | General Purpose Digital Isolator 3750Vrms 3 Channel 150Mbps 75kV/µs CMTI 16-SOIC (0.295", 7.50mm Width) |  | SOIC127P1030X265-16N | ADUM130E1BRWZ-ND | ADUM130E1BRWZ | Digi-Key | Analog Devices Inc.
2 | U3, U4 | General Purpose Amplifier 4 Circuit Rail-to-Rail 14-SOIC |  | SOIC127P600X175-14N | 296-43159-1-ND | OPA4192IDR | DigiKey | Texas Instruments
2 | U5, U6 | 19V Clamp 1A (8/20µs) Ipp TVS Diode Surface Mount 8-SO. No common node. |  | SOIC127P600X175-8N-B | 1655-1701-1-ND | SMDA12C | Digi-Key | SMC Diode Solutions
1 | U7 | Isolated Module DC DC Converter 2 Output 15V -15V 34mA, 34mA 4.5V - 5.5V Input |  | PDME1-S5-D15-S | 102-6323-ND | PDME1-S5-D15-S | Digi-Key | Bel Power Solutions
1 | U8 | +12 Linear Voltage Regulator IC 1 Output 500mA DPAK |  | DPAK229P991X238-3N | MC78M12BDTRKGOSCT-ND | MC78M12BDTRKG | DigiKey | onsemi
1 | U9 | -12 Linear Voltage Regulator IC 1 Output 500mA DPAK |  | DPAK229P991X238-3N | MC79M12CDTRKGOSCT-ND | MC79M12CDTRKG | DigiKey | onsemi
1 | U10 | Isolated Module DC DC Converter 1 Output 9V 111mA 4.5V - 5.5V Input |  | PDSE1-S5-S9-S | 102-6292-ND | PDSE1-S5-S9-S | Digi-Key | Bel Power Solutions
1 | U11 | +5V Linear Voltage Regulator IC 1 Output 500mA DPAK |  | DPAK229P991X238-3N | MC78M05CDTRKGOSCT-ND | MC78M05CDTRKG | DigiKey | onsemi
1 | U12 | 12 Bit Digital to Analog Converter 8 16-WQFN (3x3) |  | QFN50P300X300X80_HS-17N | 296-52288-1-ND | DAC60508MCRTET | DigiKey | Texas Instruments
1 | U13 | IC RCVR RS422 QUAD DIFF 16TSSOP |  | TSOP65P640X120-16N | 296-30088-1-ND | AM26C32IPWR | DigiKey | Texas Instruments

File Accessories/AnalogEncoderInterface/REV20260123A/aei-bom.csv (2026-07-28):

Qty | Designator | Discription | Value | Footprint | Supplier Part Number | Manufacturer Part Number | Supplier | Manufacturer
3 | C1, C2, C9 | Capacitor | 6.8uF | 1206-CAP | 445-11734-1-ND | C3216JB1H685K160AB | Digi-Key | TDK Corporation
3 | C3, C4, C7 | Capacitor | 10uF | 0805-CAP | 490-18663-1-ND | GRM21BR61H106KE43L | Digi-Key | Murata Electronics
6 | C5, C6, C10, C11, C12, C13 | Capacitor | 1uF | 0603-LED | 490-12330-2-ND | GRT188R61H105KE13D | Digi-Key | Murata Electronics
1 | C8 | Capacitor | 10uF | 0603-LED | 1276-1871-1-ND | CL10A106MP8NNNC | Digi-Key | Samsung Electro-Mechanics
2 | J1, J3 | Screw Terminal | 01x06 | TerminalBlock_Phoenix:TerminalBlock_Phoenix_MKDS-1,5-6_1x06_P5.00mm_Horizontal | 277-1581-ND | 1935200 | Digi-Key | Phoenix Contact
1 | J2 | Screw Terminal | 01x02 | CONN_1935161_PXC | 277-1667-ND | 1935161 | Digi-Key | Phoenix Contact
1 | J4 | Screw Terminal | RJ45 | Connector_RJ:RJ45_Amphenol_RJHSE5380 | 664-RJHSE5380-ND | RJHSE5380 | Digi-Key | Phoenix Contact
1 | L1 | CMC 9UH, 3.5A, 2LN, 800 Ohm | WE-SL5_HC | WE-SL5_HC | 732-2215-1-ND | 744273801 | Digi-Key | Wurth Electronics
2 | LED1, LED3 | LED | RED | 0603-LED | 160-1447-1-ND | LTST-C191KRKT | Digi-Key | Lite-On Inc.
1 | LED2 | LED | YELLOW | 0603-LED | 160-1448-1-ND | LTST-C191KSKT | Digi-Key | Lite-On Inc.
1 | PS1 | DC/DC Power Supply | RS6-2405S | CONV_RS6-2405S | 945-2985-ND | RS6-2405S | Digi-Key | Recom Power
1 | PS2 | DC/DC Power Supply | RS6-2415D | CONV_RS6-2415D | 945-2990-ND | RS6-2415D | Digi-Key | Recom Power
1 | R2 | Resistor | 70R | 1206-RES | Y162570R0000A9W-ND | Y162570R0000A9W | Digi-Key | VPG Foil Resistors
3 | R3, R4, R5 | Resistor | 3k | 0603-RES | RMCF0603FT3K00CT-ND | RMCF0603FT3K00 | Digi-Key | Stackpole Electronics Inc
4 | standoff1, standoff2, standoff3, standoff4 | Mounting Standoffs for Board | #4-40 1/2" |  | 36-1656-ND | 1656 | Digi-Key | Keystone Electronics
4 | screw1, screw2, screw3, screw4 | Mounting Screws for Board | #4-40 1/4" |  | 36-9900-ND | 9900 | Digi-Key | Keystone Electronics
18 | TP1,TP2,TP3,TP4,TP5,TP6,TP7,TP8, TP10, TP11, TP12, TP13, TP14, TP15, TP16, TP17, TP18, TP19 | Test Point, Yellow, 1-Pin THD, RoHS, Bulk |  | KSTN-5004 | 36-5004-ND | 5004 | Digi-Key | Keystone
2 | U1, U2 | IC OPAMP DIFF 2 CIRCUIT 14SOIC | INA2143U | INA2143U:D14 | INA2143U-ND | INA2143U | Digi-Key | Texas Instruments
1 | U3 | IC REG LINEAR 1.5V 3A DDPAK-5 | LT1764EQ-1.5-PBF | LTI1764EQ:DDPAK-5_Q_LIT | LT1764EQ-1.5#PBF-ND | LT1764EQ-1.5#PBF | Digi-Key | Analog Devices Inc.
1 | VR1 | TRIMMER 10K OHM 0.5W PC PIN TOP | 10 K | TRIM_3362P-1-103LF | 3362P-103LF-ND | 3362P-1-103LF | Digi-Key | Bourns Inc.

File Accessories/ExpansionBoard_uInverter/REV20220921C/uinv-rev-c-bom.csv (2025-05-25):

Quantity | Designator | Description | Value | Footprint | Supplier Part Number | Manufacturer Part Number | Supplier | Manufacturer
3 | C1A, C1B, C1C | Cap Ceramic 0.1uF 35V X7R 10% SMD 0805 | 100nF | 0805_CAP | 399-17618-1-ND | C0805C104K6RACTU | DigiKey | KEMET
5 | C2A, C2B, C2C, C5, C6 | 0805 35 V 10 uF ±10% Tolerance X5R Multilayer Ceramic Capacitor | 10uF | 0805_CAP | 490-10514-2-ND | GRM21BR6YA106KE43L | DigiKey | Murata
6 | C3A, C3B, C3C, C4A, C4B, C4C | 2.2 µF ±10% 35V Ceramic Capacitor X7R 0805 | 2.2uF | 0805_CAP | 445-7551-1-ND | C2012X7R1V225K125AB | DigiKey | TDK
2 | C7, C8 | Cap Aluminum 1000uF 35V 20% (12.5 X 25mm) Radial 5mm 3190mA 7000 hr 105C Ammo Pack | 1mF | CAP_PAN_12.5X25_PAN | P19719CT-ND | EEU-FM1V102B | DigiKey | Panasonic
1 | C9 | Capacitor 0.1uF 16V 0805 SMD X7R | 100nF | 0805_CAP | 311-1142-1-ND | CC0805KRX7R7BB104 | DigiKey | Yageo
1 | CONN1 | CONN PWR JACK 2X5.5MM SOLDER |  | CUI_PJ-037AH | CP-037AH-ND | PJ-037AH | DigiKey | CUI
1 | CONN2 | Conn High Density D-Sub SKT 15 POS 2.28mm Solder RA Thru-Hole 15 Terminal 1 Port |  | ICD15S13E6GV00LF | 609-2802-ND | ICD15S13E6GV00LF | DigiKey | Amphenol FCI
1 | CONN3 | CONN MOD JACK 8P8C R/A SHIELDED |  | CONN_RJSAE538502_AMP | RJSAE-5385-02-ND | RJSAE-5385-02 | DigiKey | Amphenol Commercial
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

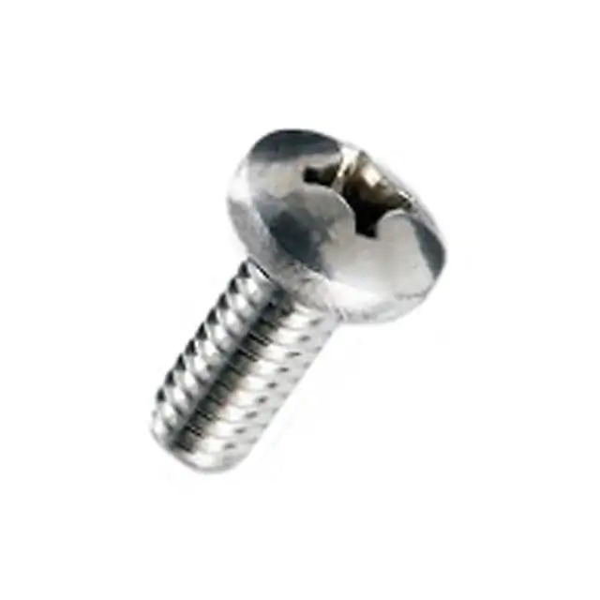
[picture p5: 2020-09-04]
Accessories/ExpansionBoard_DAC/altium/parts/screw-4-40.jpg

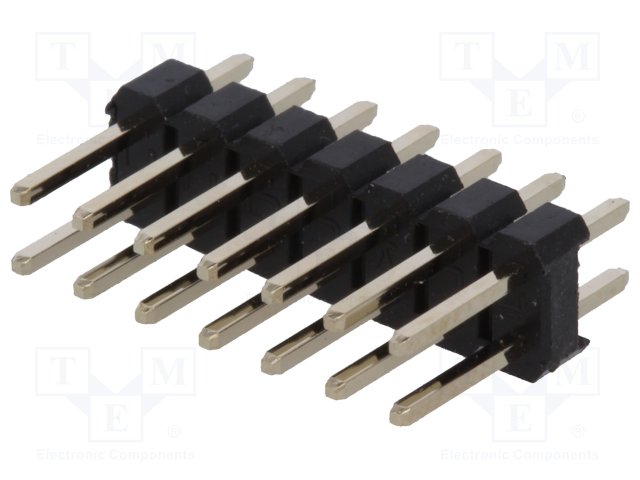
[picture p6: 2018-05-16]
altium/parts/2x7.jpg

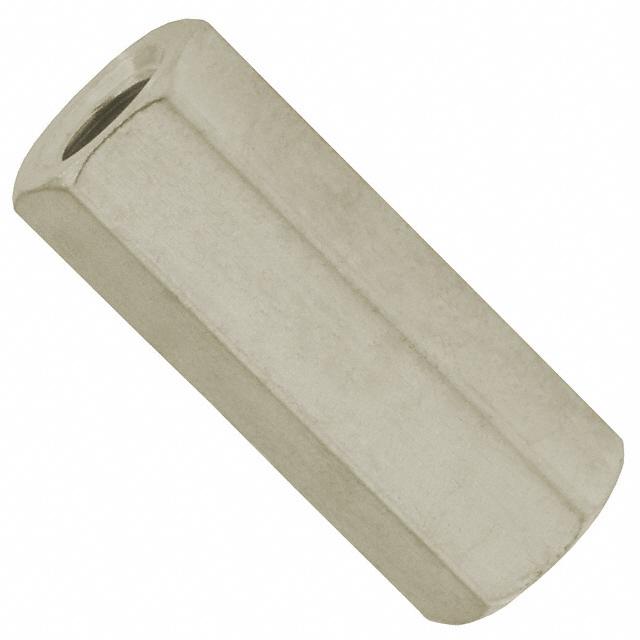
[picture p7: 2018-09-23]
altium/parts/standoff-4-40.jpg

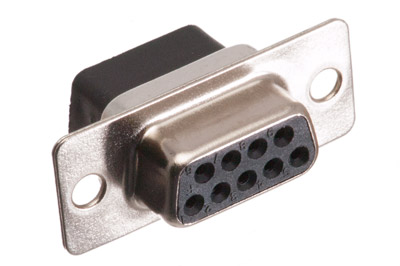
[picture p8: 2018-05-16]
altium/parts/DB9.jpg

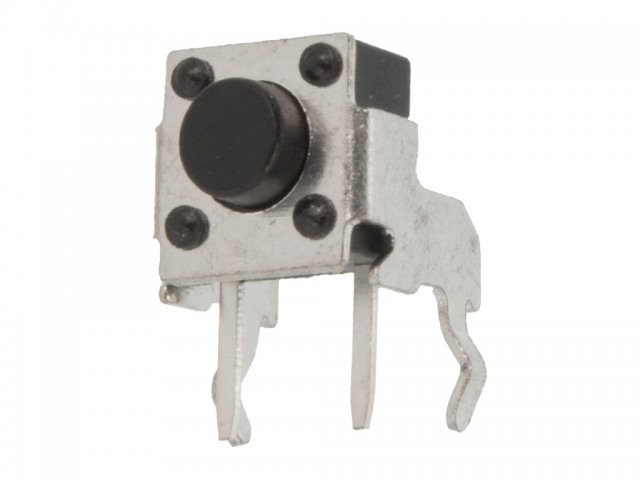
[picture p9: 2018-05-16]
altium/parts/button.jpg

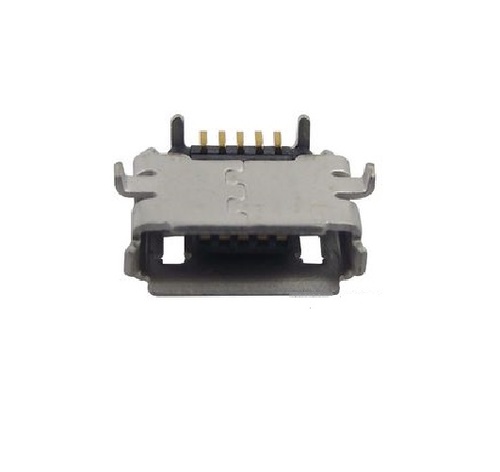
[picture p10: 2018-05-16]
altium/parts/micro_usb_smd.jpg

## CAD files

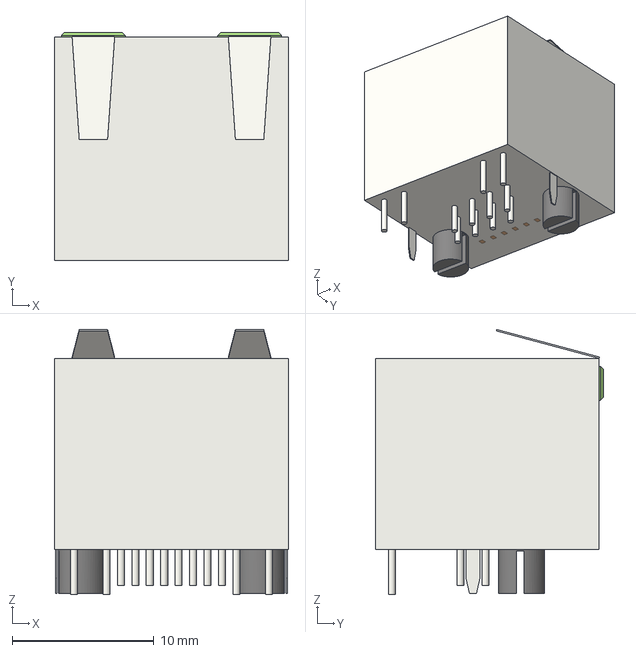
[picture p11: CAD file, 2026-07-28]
Accessories/AnalogEncoderInterface/kicad/3d-models/RJ45_Amphenol_RJHSE538X.step
16.5 x 16.1 x 18.7 mm

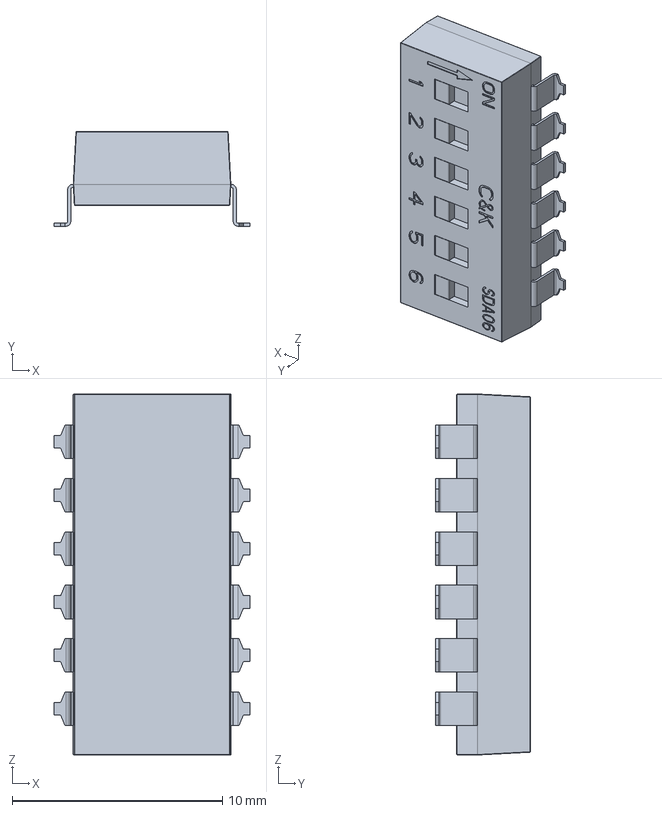
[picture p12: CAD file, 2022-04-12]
Accessories/ExpansionBoard_DAC/STEP Files/SDA06H0SBR.stp
9.30 x 4.50 x 17.2 mm

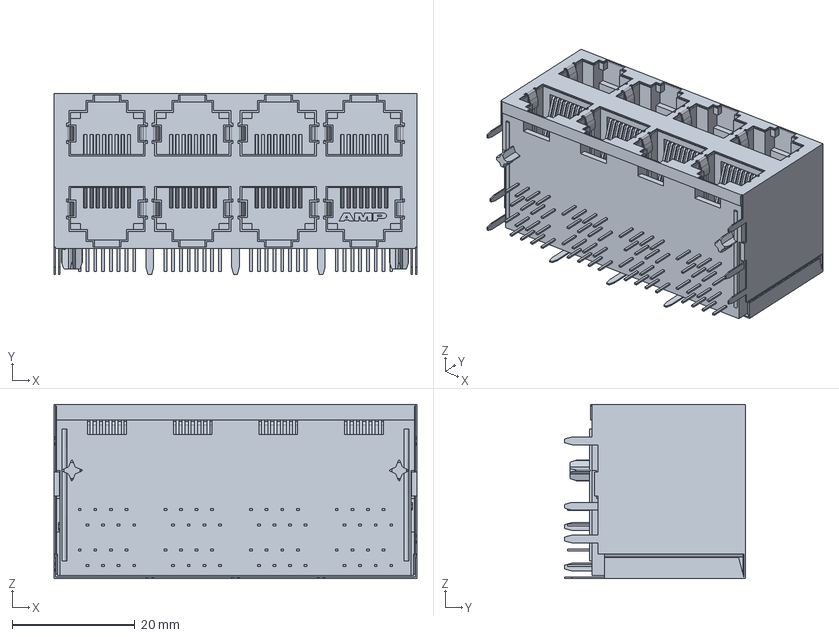
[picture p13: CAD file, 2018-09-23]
STEP Files/c-5569257-1-a1-3d.stp
59.2 x 29.5 x 28.4 mm

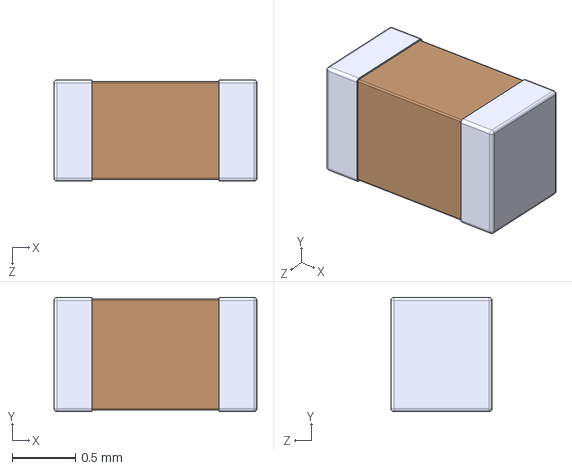
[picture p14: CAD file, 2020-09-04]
Accessories/ExpansionBoard_DAC/STEP Files/CL10B105MO8NNWC--3DModel-STEP-56544.STEP
1.60 x 0.9 x 0.8 mm

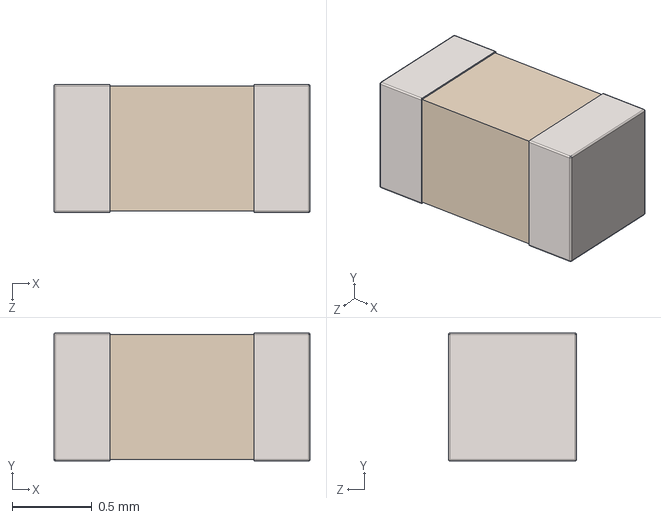
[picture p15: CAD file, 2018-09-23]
STEP Files/0603cap.step
1.60 x 0.8 x 0.8 mm

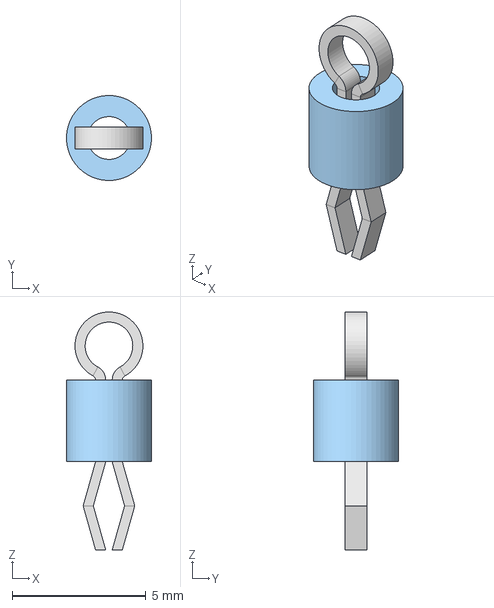
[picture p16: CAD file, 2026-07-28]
Accessories/AnalogEncoderInterface/kicad/3d-models/TestPoint_Keystone_5005-5009_Compact.step
3.18 x 3.18 x 8.90 mm

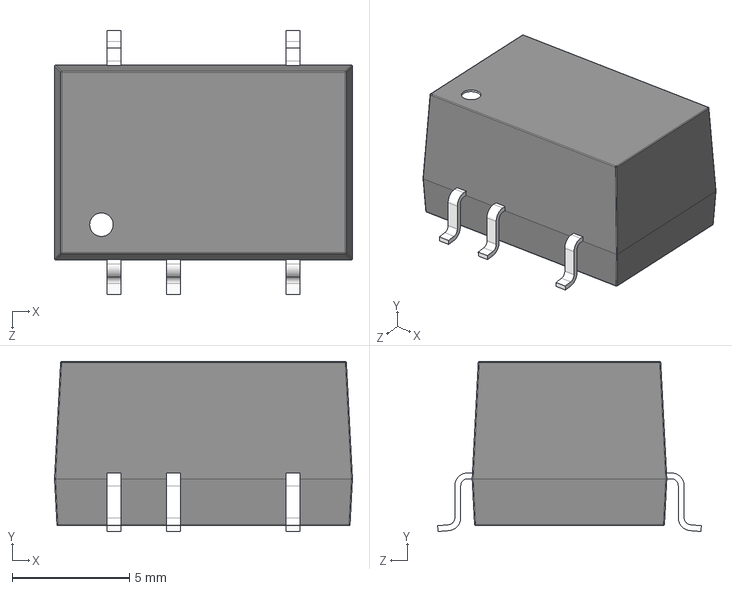
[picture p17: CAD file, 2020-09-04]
Accessories/ExpansionBoard_DAC/STEP Files/CUI_PES1-S5-S9-M.step
12.7 x 7.25 x 11.2 mm

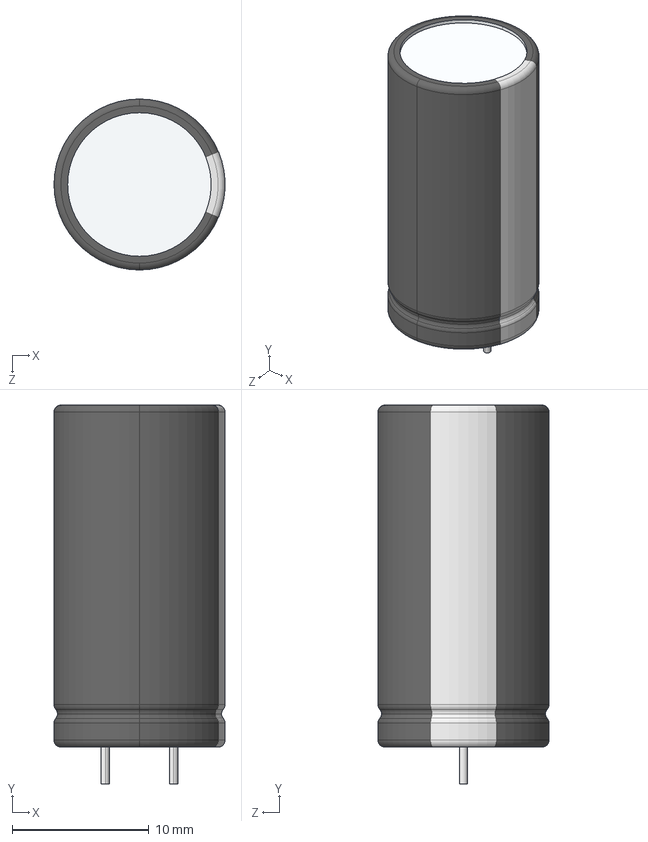
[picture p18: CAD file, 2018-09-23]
STEP Files/cap-uvr1h102mhd1to.step
12.5 x 27.7 x 12.5 mm

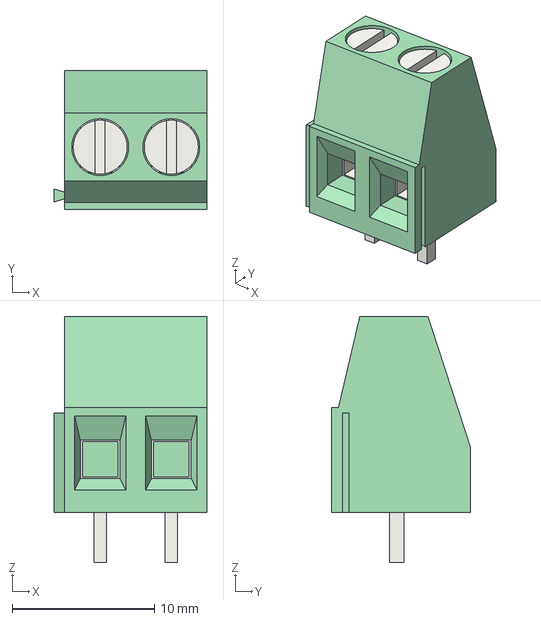
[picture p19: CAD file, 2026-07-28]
Accessories/AnalogEncoderInterface/kicad/3d-models/TerminalBlock_Phoenix_MKDS-1,5-2_1x02_P5.00mm_Horizontal.step
10.7 x 9.80 x 17.3 mm

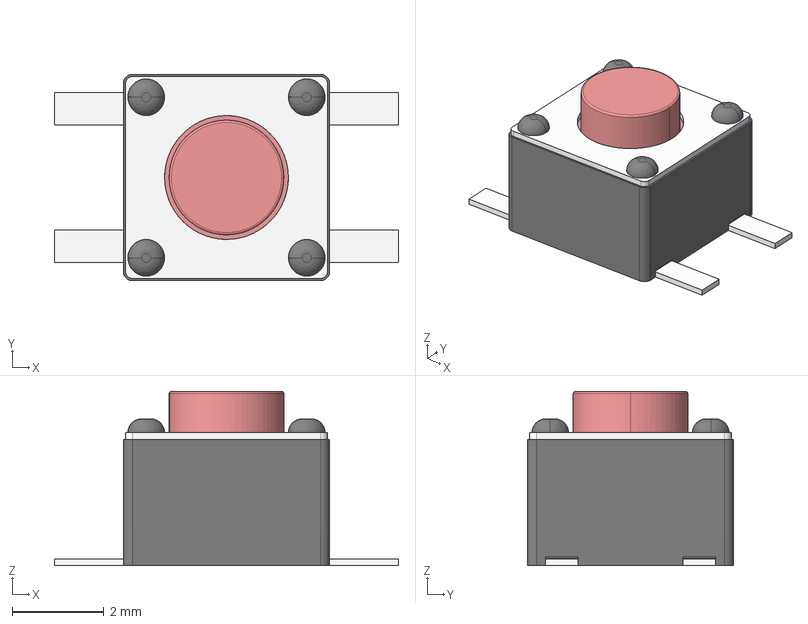
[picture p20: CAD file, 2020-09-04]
Accessories/ExpansionBoard_DAC/STEP Files/Tact Switch SMD 4.5x4.5mm.stp
7.50 x 4.50 x 3.80 mm

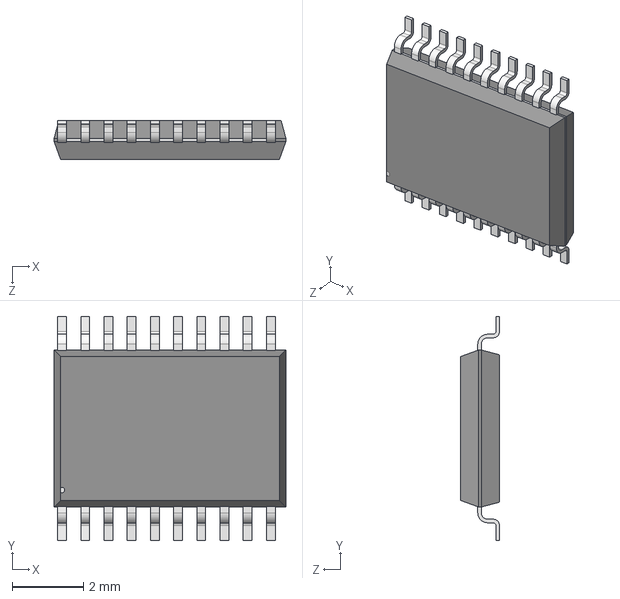
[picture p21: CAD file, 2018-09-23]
STEP Files/TSSOP20.step
6.50 x 6.28 x 1.09 mm

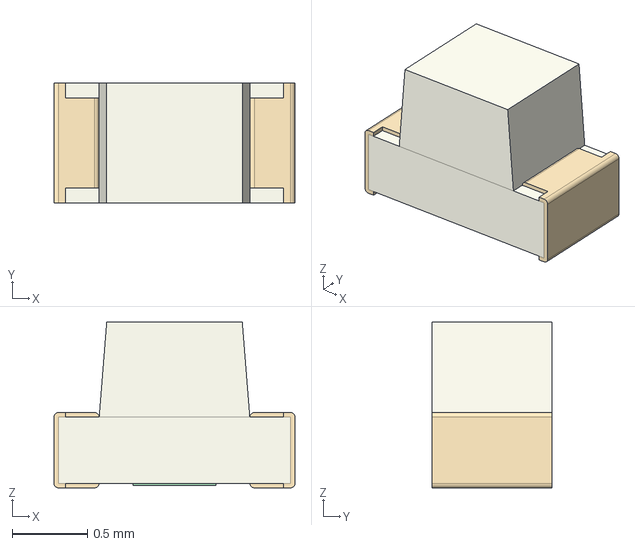
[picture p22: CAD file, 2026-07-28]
Accessories/AnalogEncoderInterface/kicad/3d-models/LED_0603_1608Metric.step
1.60 x 0.8 x 1.10 mm

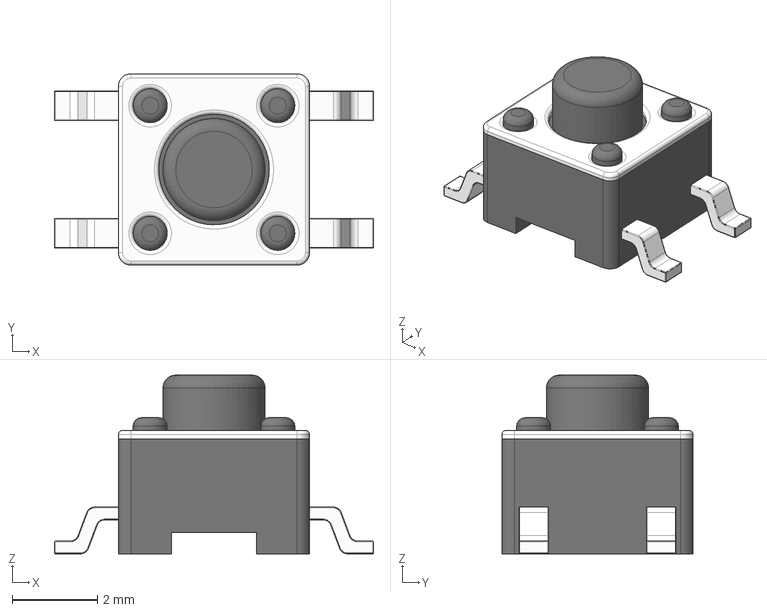
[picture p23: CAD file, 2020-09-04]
Accessories/ExpansionBoard_DAC/STEP Files/Tact Switch 4.5mm SMT.step
7.50 x 4.50 x 4.20 mm

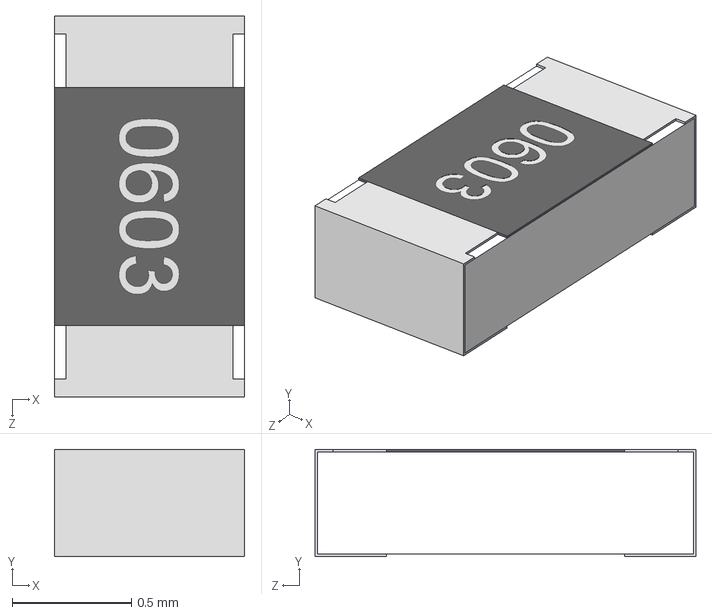
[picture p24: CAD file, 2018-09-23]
STEP Files/0603res.step
0.8 x 0.45 x 1.60 mm

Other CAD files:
Accessories/AnalogEncoderInterface/kicad/3d-models/INA2143U.STEP
Accessories/ExpansionBoard_DAC/STEP Files/CUI_PES1-S5-D24-M.step
STEP Files/soic16.step
Accessories/AnalogEncoderInterface/kicad/3d-models/RS6-2415D--3DModel-STEP-1.STEP
Accessories/AnalogEncoderInterface/kicad/3d-models/3362P-1-103LF.STEP
Accessories/AnalogEncoderInterface/kicad/3d-models/C_0603_1608Metric.step
Accessories/AnalogEncoderInterface/kicad/3d-models/C_1206_3216Metric.step
Accessories/AnalogEncoderInterface/kicad/3d-models/LT1764EQ-1.5#PBF.STEP
Accessories/AnalogEncoderInterface/kicad/3d-models/RS6-2405S--3DModel-STEP-1.STEP
Accessories/AnalogEncoderInterface/kicad/3d-models/R_0603_1608Metric.step
Accessories/AnalogEncoderInterface/kicad/3d-models/R_1206_3216Metric.step
Accessories/AnalogEncoderInterface/kicad/3d-models/TerminalBlock_Phoenix_MKDS-1,5-6_1x06_P5.00mm_Horizontal.step
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

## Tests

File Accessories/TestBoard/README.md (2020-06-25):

# AMDC Test Board

This subfolder houses all the design files for the AMDC Test Board, an accessory for the AMDC which is designed to aid in testing the Power Stack and Analog interfaces. This board plugs into the AMDC.

## Documentation

Read about the design of this test board in the [docs folder...](docs/)

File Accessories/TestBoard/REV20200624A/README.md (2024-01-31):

# AMDC Test Board REV20200624A

This folder contains the compiled design outputs for the AMDC Test Board REV A (design frozen on June 24, 2020). This includes the schematics, images of the PCB layout, the bill of materials (BOM), and the files needed to order boards from fab houses (gerbers).

## PCB Properties

| Question | Answer |
|---|---|
| Board Size (H x W) | 3" x 3.9" |
| Numer of Layers | 2 |
| Number of Holes | 184 |
| Number of Slots/Cutouts | 0 |
| Surface Finish | Tin Lead (HASL)  |
| Silkscreen | Both Sides |
| Copper Weight | 1oz |
| Trace Width / Spacing | 6/6mil |
| Min Drill | 14mil |

## Recommended Cables

This test board requires cables to interface to the AMDC power stack and analog interface ports. The following are the recommended cables to buy.

### Power Stack Cables



Digi-Key Part Number: `CS-DSDHD15MM0-002.5-ND`

Only one cable is required.

### Analog Cables



Digi-Key Part Number: `MP-6ARJ45SNNK-001-ND`

Four (4) cables are required.

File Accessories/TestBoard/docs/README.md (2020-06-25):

# AMDC Test Board

This document describes the design considerations and implementation details for the AMDC test board, which is an accessory board which plugs into the AMDC to test the functionality of the power stack and analog interfaces.

## Relevant Hardware Versions

Test Board: REV A, AMDC: REV D

## Purpose

The AMDC Test Board serves two purposes:

1. Test newly fabricated AMDCs to verify PWM and analog I/O are functional.
2. Act as breakout board for learning the AMDC peripherals (i.e. AMDC Labs).

## Features

The test board interfaces the inverter output port to the analog input port. It provides thefollowing features:

1. Six RC filters on each of the six PWM outputs (bandwidth set to 10kHz)
2. Four LEDs for each of the four status lines
3. Loopback capability for status lines (they can be input or output to AMDC)
4. One BNC connector to measure filtered PWM voltage (jumpers can select one of six filtered PWM)
5. Two power LEDs (VDD and VPS)
6. Test points on all important signals
7. Both positive and negative analog voltage inputs to the AMDC
8. +/- 10V input to AMDC (to test full input range)

## Testing Capability

Tests that can be conducted using the Test Board:

#### AMDC Power Stack Interface

1. Verify VDD power
2. Verify status lines as outputs
3. Verify status lines as inputs
4. Verify PWM duty ratio output

#### AMDC Analog Inputs

1. Verify both positive and negative voltage input
2. Verify full range +/- 10V input
3. Explicitly verify +15V rail
4. Implicitly verify -15V rail

## PCB

Designed to be cheap to fabricate:

- 2-layer, 3" x 3.9"
- Parts only on top layer (no silkscreen on bottom)
- BOM: $25 in single quantity

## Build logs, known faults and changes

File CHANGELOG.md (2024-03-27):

# AMDC Changelog

This file describes any key changes between hardware revisions.

## [REV20231005F](https://github.com/Severson-Group/AMDC-Hardware/milestone/8)

- Add termination resistors for incoming GPIO signals ([#226](https://github.com/Severson-Group/AMDC-Hardware/issues/226))
- Fix pull-down resistor strength to hold PWM gate signals low during boot-up ([#227](https://github.com/Severson-Group/AMDC-Hardware/issues/227))
- Fix footprints ([#211](https://github.com/Severson-Group/AMDC-Hardware/issues/211))
- Fix part numbers ([#189](https://github.com/Severson-Group/AMDC-Hardware/issues/189))

## [REV20210325E](https://github.com/Severson-Group/AMDC-Hardware/milestone/5)

- Remove isoSPI ([#141](https://github.com/Severson-Group/AMDC-Hardware/issues/141))
- Add shared UART and JTAG interface ([#158](https://github.com/Severson-Group/AMDC-Hardware/issues/158))
- Add more GPIO ports ([#140](https://github.com/Severson-Group/AMDC-Hardware/issues/140))
- Add mechanical parts to BOM ([#115](https://github.com/Severson-Group/AMDC-Hardware/issues/115))
- Add website to PCB silkscreen ([#173](https://github.com/Severson-Group/AMDC-Hardware/issues/173))
- Add reset signal pull-up and ESD protection ([#165](https://github.com/Severson-Group/AMDC-Hardware/issues/165))
- Add local decoupling to VREF ([#171](https://github.com/Severson-Group/AMDC-Hardware/issues/171))
- Add local decoupling to 2.048V ([#170](https://github.com/Severson-Group/AMDC-Hardware/issues/170))
- Add E-STOP logic signal to FPGA ([#160](https://github.com/Severson-Group/AMDC-Hardware/issues/160))
- Add PTC resettable fuses to PWM outputs ([#157](https://github.com/Severson-Group/AMDC-Hardware/issues/157))
- Add VDRIVE signal to PS interface ([#126](https://github.com/Severson-Group/AMDC-Hardware/issues/126))
- Add jumpers for default VDRIVE and ESTOP ([#102](https://github.com/Severson-Group/AMDC-Hardware/issues/102))
- Add pull-down to VCCIO_EN ([#121](https://github.com/Severson-Group/AMDC-Hardware/issues/121))
- Change power wiring in schematics ([#174](https://github.com/Severson-Group/AMDC-Hardware/issues/174))
- Change shield termination to VIN- ([#156](https://github.com/Severson-Group/AMDC-Hardware/issues/156))
- Change mounting holes to VIN- from GND ([#169](https://github.com/Severson-Group/AMDC-Hardware/issues/169))
- Change DB15 P/N to include screw posts ([#134](https://github.com/Severson-Group/AMDC-Hardware/issues/134))
- Change to USB type B recepticle ([#101](https://github.com/Severson-Group/AMDC-Hardware/issues/101))
- Update top-level block diagram ([#164](https://github.com/Severson-Group/AMDC-Hardware/issues/164))
- Fix 24V supply to GPIO port ([#103](https://github.com/Severson-Group/AMDC-Hardware/issues/103))
- Fix power protection circuitry ([#163](https://github.com/Severson-Group/AMDC-Hardware/issues/163))
- Fix board start-up PWM issues ([#137](https://github.com/Severson-Group/AMDC-Hardware/issues/137))
- Fix P/N for RC filter caps ([#96](https://github.com/Severson-Group/AMDC-Hardware/issues/96))
- Fix BOM components for DFM ([#159](https://github.com/Severson-Group/AMDC-Hardware/issues/159))
- Fix footprints ([#95](https://github.com/Severson-Group/AMDC-Hardware/issues/95), [#128](https://github.com/Severson-Group/AMDC-Hardware/issues/128))

## [REV20200129D](https://github.com/Severson-Group/AMDC-Hardware/milestone/4)

- New PCB form factor (6" x 6.75", 6 layers)
- Add power stack supply rail distribution
- Add isoSPI ports
- Add extra encoder port
- Add 0R resistors to subsection power for debugging
- Add 100k resistors across analog inputs
- Add serially addressable RGB LEDs
- Add EEPROM
- Add fiducials to layout
- Remove user button / switch
- Remove discrete RGB LED
- Remove ADC2, now just one ADC
- Remove unity gain op-amp driving ADC inputs
- Reduce bulk input
- Reduce 24V power filter component current ratings
- Reduce 3V3 LDO current rating
- Change level-shifter IC for UART signals
- Change JTAG to NC module
- Change JTAG pin headers to pads
- Change values for inrush limiting circuitry
- Change FPGA driven MOSFETs to lower Vth
- Change FPGA pin-out mapping
- Change power stack connector I/O
- Change encoder input signal chain
- Change Ethernet routing to correct diff. impedance
- Fix footprints

## [REV20181121C](https://github.com/Severson-Group/AMDC-Hardware/milestone/3)

- Add inrush current limiting to 5V5 rail
- Add more silkscreen labels
- Add test points
- Change ADC reference from 2.5V to 2.048V
- Change trim resistors for +/-16V DC/DCs
- Swap UART Tx / Rx pins
- Separate power stack shields between connectors
- Fix footprints

## [REV20180717B](https://github.com/Severson-Group/AMDC-Hardware/milestone/2)

- Add power input protection
- Add test points
- Add TVS to analog inputs
- Change power input DC/DC modules
- Fix BOM with correct part numbers
- Fix footprints
- 
## REV20180525A

- Initial design

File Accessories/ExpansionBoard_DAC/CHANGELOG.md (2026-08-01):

# DAC Board Changelog

This file describes any key changes between hardware revisions.

## [REV20262707D](./REV20262707D/)

- Fix an incorrect footprint on the U9 negative voltage linear regulator ([#244](https://github.com/Severson-Group/AMDC-Hardware/issues/244))

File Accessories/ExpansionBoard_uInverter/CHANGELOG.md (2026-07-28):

## [REV20220921C](https://github.com/Severson-Group/AMDC-Hardware/tree/develop/Accessories/ExpansionBoard_uInverter/REV20220921C)

- Fix silkscreen designators ([#199](https://github.com/Severson-Group/AMDC-Hardware/issues/216))

## [REV20220329B](https://github.com/Severson-Group/AMDC-Hardware/tree/develop/Accessories/ExpansionBoard_uInverter/REV20220329B)

- Add two small (10 uF) ceramic capacitors for DC link ([#199](https://github.com/Severson-Group/AMDC-Hardware/issues/199))
- Add low pass filter capacitor at DC bus voltage sensing point ([#192](https://github.com/Severson-Group/AMDC-Hardware/issues/192))
- Add parallel decoupling capacitance as suggested in [Gate Driver](https://www.digikey.com/en/products/detail/ixys-integrated-circuits-division/IXDN614CI/2424705) datasheet
- Fix BOM with correct part number for DC bus voltage potential devider resistors ([#194](https://github.com/Severson-Group/AMDC-Hardware/issues/194))
- Improve board layout and PCB layout
- Reverse current sensing differential amplifier input polarity ([#193](https://github.com/Severson-Group/AMDC-Hardware/issues/193))
- Remove screw connectors and provide cutout in PCB for current sensing ([#197](https://github.com/Severson-Group/AMDC-Hardware/issues/197))
- Replace SMD components with 0603 size by 0805 sized components

## [REV20210506A](https://github.com/Severson-Group/AMDC-Hardware/tree/develop/Accessories/ExpansionBoard_uInverter/REV20210506A)

- Initial design

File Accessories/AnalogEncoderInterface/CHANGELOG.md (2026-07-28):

## [REV20260123A](https://github.com/Severson-Group/AMDC-Hardware/tree/develop/Accessories/AnalogEncoderInterface/REV20260123A)

- Initial design

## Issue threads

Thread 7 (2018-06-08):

Increase routing clearances for lower cost PCB manufacturing

npetersen2, 2018-06-08:
REV20180525A PCB was designed with 6/6 mil clearances, but this is probably unnecessary.

From quick looking: ADC ICs and the USB-UART IC are both QFN packages, so have smallest clearances. They should be fine at 8 mil clearances.

**I think the whole board should be adjusted to 8/8 mil clearances to reduce price.**

npetersen2, 2019-09-02:
REV C hardware was drawn with 5/5mil spacing...

As most every board house can do 6/6mil spacing for cheap, please use this for REV D layout.

npetersen2, 2019-12-09:
Using 6/6 mil clearance on REV D (and 6 layers). This should be fairly cheap for most board houses to make (especially China board houses!)

Closed 2019-12-09.

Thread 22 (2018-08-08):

U4 footprint is incorrect

jjsylvestre, 2018-08-08:
Part does not fit on current footprint. Footprint pitch is too small

Closed 2018-09-23.

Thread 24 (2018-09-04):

Switch User I/O connections from MIO bank 500 to 501

jtcomp, 2018-09-04:
The eMMC currently shares the MIO bank 500 (MIO 0 , 15:9) with some of the user I/O and the eMMC is by default connected. Many of the Bank 501 MIO pins are currently unsued (MIO 51:40), and the user I/O nets could be connected there instead.

npetersen2, 2018-09-20:
I agree this should be done... The only issue is that routing was much easier to MIO bank 500, not 501.

From what I can tell, the eMMC will be used to boot board eventually (non-volatile; can just power-up and go). I think it is only used for booting, so in theory, it is fine to share pins with user I/O, but just to be safe, probably should move to MIO bank 501, as they are unused anyway.

npetersen2, 2018-11-16:
Moved to bank 501 MIO pins.

Closed 2018-11-16.

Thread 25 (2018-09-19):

Inverter DB15 connectors too close together

npetersen2, 2018-09-19:
The stacked dual DB15 connectors for the inverter control outputs are too close together.
If you try and plug in two cables right next to each other, the cable cases hit.

To fix, increase pitch between DB15 stacks a bit. (Need to figure out how much).

npetersen2, 2019-12-09:
Fixed on REV D

Closed 2019-12-09.

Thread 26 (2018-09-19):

Add more silkscreen labels for voltage inputs

npetersen2, 2018-09-19:
Currently, board doesn't say what voltage input it needs...

Add big silkscreen labels for voltage inputs, e.g:
24V for main power
15V for VDRIVE

npetersen2, 2018-09-23:
Added silkscreen labels for correct voltage inputs:

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

Closed 2018-09-23.

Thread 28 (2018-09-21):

Verify ADC SCK signal can toggle at 100MHz on PCB trace

npetersen2, 2018-09-21:
To enable the full 1.5Msps of the LTC2320-14 ADCs, the SCK line needs to run at 100MHz.

The PL can easily generate this, and I already have verilog which works in simulation for driving ADCs.

*However*, I'm very worried about the PCB trace for SCK and really don't think it will support that high of frequency switching... It is ~6" long and not resistor terminated. We need to do experiments to see what the max frequency the current hardware supports, and then make design changes if necessary.

npetersen2, 2018-10-10:
Tips from Shanker:

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

npetersen2, 2018-11-15:
Did some looking into this... Below are two captures which show that signal integrity is not an issue. Both SCK and CLKOUT look usable at 100MHz, which will enable full ADC throughput.

First is plot of SCK from FPGA, probed at ADC. This is what controls ADC. Notice the near 0.5V overshoot on the 1.8V logic lines. Also, notice the overshoot at the end, which probably will appear as another SCK edge (but not harmful for anything).

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

Second is plot of CLKOUT from ADC, probed at FPGA. This is what FPGA will use to latch in SDO data bits. Less overshoot than previous plot.

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

Closed 2018-11-15.

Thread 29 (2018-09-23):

Fix Altium schematic templates

npetersen2, 2018-09-23:
The Altium templates are currently stored locally on the engineer's PC. They should be included in the project.

npetersen2, 2018-09-23:
After looking around, it seems that when someone checks out the project, they'll need to update the template file because Altium can't use project-relative paths.

This is fairly simple:
1. Open all schematic documents _EXCEPT PicoZed.Schdoc_
2. Under "Design->Templates->Project Templates" select "Choose a File..." and choose {Project Root}\altium\templates\A4_WEMPEC.SchDot
3. Under "Choose Document Scope" select "All open schematic documents"
4. Under "Choose Parameter Actions" select "Do not update any parameters"
5. Click "OK"

Fixing PicoZed.SchDoc: This sheet is too big to use the A4 template. To fix:
1. Open PicoZed.SchDoc
2. Under Properties -> Page Options, select Custom tab
3. Width: 17000mil, Height: 10000mil, Orientation: Landscape, Uncheck "Title Block"
4. Under Margin and Zones: Select "Show Zones", Vertical: 5, Horizontal: 5, Origin: Upper Left, Margin Width: 200mil

Closed 2018-09-23.

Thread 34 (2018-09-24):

Add test points to ADC serial digital interface for debugging

npetersen2, 2018-09-24:
Put test points on all serial data lines that interface with the ADCs. These will help us analyze signal integrity issues etc.

npetersen2, 2018-09-24:
ADC1 done:

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

npetersen2, 2018-09-25:
After more thought, these test points should be directly inline with the traces, not branching off and up. I think this will reduce signal integrity issues from ringing.

I will redo layout and post another picture.

npetersen2, 2018-09-26:
I think this is better. Now to do same thing for ADC2.

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

npetersen2, 2018-09-27:
ADC2 done:

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

npetersen2, 2018-09-27:
That should be good. Closing issue.

npetersen2, 2018-09-27:
Whoops... Long side of test point pad is the open part of the metal loop for clamping on test lead.

For layout, either the test points need to be rotated 90 degrees so that long side is open, or spaced with larger pitch between them.

npetersen2, 2018-09-28:
Alright, I think v3 of the test points is a winner:

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

Closed 2018-09-28.

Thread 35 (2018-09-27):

Consider power sequencing to fix inrush current issues

npetersen2, 2018-09-27:
Reduced bulk capacitance on VIN to 1000uF. This solved PicoZed "blinky" issue (reduced inrush current).

"If I have the powerstack connected when I power the AMDC up, the inrush from the powerstack seems to still be causing blinky. May need to implement some sort of power sequencing on rev 3. I'll think about it" -Jason.

This issue serves as a reminder for this problem.

jjsylvestre, 2018-10-01:
Powered up board, then connected 5V5 jumper per Eric's recommendation. Same results - blinky

jjsylvestre, 2018-10-01:
Inrush current on 5V5 node
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

jjsylvestre, 2018-10-01:
Solved problem by adding 2ohm resistor inline with 5V5 node to limit inrush current

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

npetersen2, 2018-10-01:
@jjsylvestre Can you decide how we should fix this on REV C and file a bug issue describing what should be done (and close this issue)? Thanks.

jjsylvestre, 2018-10-02:
See Issue #43 for continued conversation on this

Closed 2018-10-02.

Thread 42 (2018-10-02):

Too much inrush current on 5V5 from Picozed

jjsylvestre, 2018-10-02:
Proposed solution is current limiting resistor with SPST relay in parallel that close from an enable signal from the PicoZed

jjsylvestre, 2018-10-02:
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

npetersen2, 2018-11-13:
Talked with @jjsylvestre:

Would like the PZ_ENABLE signal in above picture to not be controlled from software, but instead in h/w.

Our idea: use a RC circuit with time constant of ~1 sec, feeding into a comparator, which then drives a n-channel MOSFET to enable relay, thus shorting out inrush limiting resistor.

I'll implement this idea and post again for discussion.

npetersen2, 2018-11-14:
**Proposed implementation:**
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

Need to pick relay to use, add flyback diode, and add LED to indicate when resistor is inline.

@jjsylvestre thoughts?

npetersen2, 2018-11-15:
Thinking that main resistor should be 2 ohms (not 1), due to power supply limit of 3A at 5.5V.

This would limit current to 2.75A, and require a (2.75)^2 * 2 = ~15W resistor... Pretty beefy.

jjsylvestre, 2018-11-15:
Looks good.  Looks like comparator is TTL output. Are you 100% certain that when IN+ > IN-, that corresponds to a high output? Couldn't find that info in the ds.

As for the power value of the resistor, we can probably some get away with something lower since the current is exponentially decaying with time.

Also, we might want to take a look at the 5V rail during the startup event to see how stable it is.

npetersen2, 2018-11-16:
- Changed comparator to one that specified its output level vs. input voltages (LMV761MAX/NOPB)
- Added flyback diode
- Using four 2512 SMD 6.8R resistors in parallel to achieve high max power, while being cheap and relatively small footprint.

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

npetersen2, 2018-11-16:
Last thing is to check 5V rail during startup to see that it is stable enough to use for cap charging / timing. Will update issue with results.

npetersen2, 2018-11-16:
Plot of 24V board input (C2) vs. 5V rail (C1) during startup. Looks good to me.

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

npetersen2, 2018-11-17:
Reopening for investigation on not using mechanical relay. Maybe use BJT? Currently looking up ANs for ideas.

See this article about why FPGA startup is typically an issue for power supplies:
http://www.ti.com/lit/an/slyt079/slyt079.pdf

npetersen2, 2018-11-17:
This paper describes how to design MOSFET-based inrush current limiter:
http://www.mosaic-industries.com/embedded-systems/_media/pdfs/application-notes/motorola-an1542-active-inrush-current-limiter.pdf

npetersen2, 2018-11-17:
Final implementation: using TPS22965 (http://www.ti.com/lit/ds/symlink/tps22965.pdf), costs $1.

This is a 5.7-V, 6-A, 16-mΩ On-Resistance Load Switch. Basically just an n-channel MOSFET which has an adjustable slew rate for turn on.

This slew rate determines inrush current. I think the only capacitance on the 5.5V node is the bypass caps for the LDOs. Therefore, this is 50uF. I calculated values resulting in inrush of ~700mA.

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

Closed 2018-11-17.

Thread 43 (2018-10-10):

Test GPIO

npetersen2, 2018-10-10:
We need to verify that the GPIO circuitry works before ordering REV C:

Direction signal set via hardware jumper:
- [x] Verify GPIOA/B[5..12] works as both 3.3V and 5V output
- [ ] Verify GPIOA/B[5..12] works as both 3.3V and 5V input

Direction signal set via firmware:
- [ ] Verify GPIOA/B[1..4] works as both 3.3V and 5V output
- [ ] Verify GPIOA/B[1..4] works as both 3.3V and 5V input

npetersen2, 2018-10-10:
GPIOA/B[5..12] works as expected for output, except GPIO_9A. The breakout board LED always stays off, so this could be an assembly issue. Check continuity along signal path to check for bad connections.

npetersen2, 2018-11-19:
Checked continuity of signal along PCB. Looks like it comes out of FPGA at 1.8V and arrives at input of level-shifter, but doesn't appear at output. Probably a broken channel on the chip.

No need to replace on REV B PCB. Issue will probably go away on REV C due to new parts.

npetersen2, 2019-02-20:
Closing this issue as it doesn't fit the way GitHub Issues should be used... Testing is not an Issue.

Closed 2019-02-20.

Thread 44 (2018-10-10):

Investigate PWM VDRIVE level shifter issue

npetersen2, 2018-10-10:
The second stage level shifter for the PWM outputs (5V to VDRIVE) keeps breaking itself and melting.

We need to investigate this issue, as it has happened 3 or 4 times now.

npetersen2, 2019-12-09:
Hasn't happened since the first issues... Claiming this isn't an issues anymore, closing.

Closed 2019-12-09.

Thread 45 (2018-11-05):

Change ADC pseudo-differential reference point from 2.5V to 2.048V

npetersen2, 2018-11-05:
The ADCs are used in a pseudo-differential configuration, meaning that the Vin to be measured swings between 0V to some max, notably not below 0V. Vin goes to the ADC V+ input, while a fixed reference goes to ADC V-. Therefore, ADC measures Vin - Vref.

ADC full-scale voltage is configured to be internal reference buffer of 4.096V. Therefore, for symmetrical input range, the reference point should be Vadc,ref / 2, or 2.048V. Current design has Vref = 2.5V.

To fix, change schematic in Power_REF_2V5.SchDoc. Replace U45, LT1461CCS8-2.5#PBF, with MCP1501:
- http://ww1.microchip.com/downloads/en/DeviceDoc/20005474E.pdf
- https://www.digikey.com/short/j05083

npetersen2, 2018-11-13:
Implemented in schematics.

Closed 2018-11-13.

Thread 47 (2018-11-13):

Change all analog conditioning circuitry to use single package in-amp devices

npetersen2, 2018-11-13:
@elsevers I believe we decided to just go with the single package in-amp with the fixed 0.1x gain (via laser trimmed resistors). Can you confirm? If so, I will remove the discrete op-amps and make everything this topology.

npetersen2, 2018-11-13:
I distinctly remember you agreeing to this, so I went ahead and implemented it. If you have a concern, please reopen this issue.

Closed 2018-11-13.

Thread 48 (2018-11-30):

Fix Altium P/Ns

npetersen2, 2018-11-30:
If you use Altium to generate a BOM, it works great, but many part numbers are for Digi-Reel packaging. Also, a few of the parts are unavailable on Digi-Key, but in reality, they are there just with a slightly different P/N (e.g. different temperature rating, etc).

In Altium, let's change all the P/Ns which are for Digi-Reels or unavailable to prevent spending hours trying to order the BOM.

npetersen2, 2019-12-09:
After much effort, fixed in REV D. Should be able to just export BOM from altium and click order! :)

Closed 2019-12-09.

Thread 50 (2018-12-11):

Fix component values for Power Protection circuitry

npetersen2, 2018-12-11:
On REV B and now REV C boards, we have simply shorted out the power protection circuitry to disable it because the specified resistor values don't seem to work.

It would be nice to have this added protection working for us, so we need to figure out what the values should be and update the schematics.

npetersen2, 2019-12-09:
@ASHAD1 Can you take a look at the datasheet for LTC4365 and give calculating resistor values a go? I want a second set of eyes on this since it isn't exactly trivial and I want it to work for REV D... :) Perhaps deadline by middle of week of so?

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

ASHAD1, 2019-12-09:
@npetersen2 I have looked into the datasheet, The value calculated was the same (R1 = 176.5k, R2 = 123.5k, R3 = 11.7M). We can have a working range very close to 20V -34V.
For shutdown resistor (R55) we can use a resistor in the range of 100k - 500k. Higher value, if we expect to have some transients.

npetersen2, 2019-12-15:
@ASHAD1 great thanks for the feedback. I have picked available resistors and updated design, see below. I have also removed the fault LED indicator -- during a fault, we don't have reliable power to power the LED... so no point in having a LED there! Does the schematic look good to you?

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

Closed 2020-01-14.

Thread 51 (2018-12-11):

Add pull-down resistors to RGB LED MOSFETs

npetersen2, 2018-12-11:
To prevent the RGB LED from lighting up before PicoZed is actively driving the LED enable signals, add 10k pull down resistors to each of the three RGB LED MOSFET drivers.

I reworked current REV C board to add these onto it, and it seems to work as expected (i.e. LED stays off during boot up).

See picture for details:

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

npetersen2, 2019-07-28:
Done.

Closed 2019-07-28.

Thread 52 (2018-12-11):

Update Inrush Current Limiter circuitry

npetersen2, 2018-12-11:
The calculated value for C48 was too small and still resulted in the hiccuping issue.

I stacked a 100nF cap on top of C48 on the REV C board and it fixed the issue.

We probably don't need to increase C48 all the way up to 100nF from 100pF, but it does work...

Let's update the schematics to reflect this needed change.

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

elsevers, 2018-12-11:
If the datasheet of this part requests a 100pF capacitor for reasons of ESR, etc., we may consider placing a 100 nF capacitor in parallel with the 100pF capacitor.

npetersen2, 2019-09-01:
Done.

Closed 2019-09-01.

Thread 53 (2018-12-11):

Add "INV5..8" to silkscreen

npetersen2, 2018-12-11:
REV C board doesn't have silkscreen label for Supply Voltage pin jumpers. Please add this.

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

npetersen2, 2019-12-09:
Non-issue on REV D.

Closed 2019-12-09.

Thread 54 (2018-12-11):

Replace JTAG interface with one w/o USB connector

npetersen2, 2018-12-11:
After we ordered the wrong JTAG interface (it didn't have a USB connector on it; you have to put one on the board and wire USB D+/- to the module), I realized that we should actually switch to this NC module....

If we use our own USB connector, we can shrink the amount of front board space the JTAG interface takes up to be the same as the USB OTG / UART systems. We just need to slide the JTAG module towards the middle of the board.

This will open up the required space for spreading out the stacked DB15 connectors for the inverters. See #25 for that issue.

Proposed change:
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

npetersen2, 2019-07-28:
Done.

Closed 2019-07-28.

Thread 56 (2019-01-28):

Move JP1 away from DB9 connector

npetersen2, 2019-01-28:
The JP1 header for encoder voltage selection is too close to the DB9 connector, not so much that it won't work, but just a little annoying.

Please move this up higher (~0.5"). There is ample space.

npetersen2, 2019-12-09:
Non issue on REV D.

Closed 2019-12-09.

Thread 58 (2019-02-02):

RGB LED is rather dim

npetersen2, 2019-02-02:
The PicoZed can drive the RGB and turn on each color, etc.

Issue is that the LED is very dim. I think there is an issue with the 1.8V drive voltage not sufficiently saturating the LED drive transistor base or maybe MOSFET gate...

Please look into this.

npetersen2, 2019-09-01:
Fixed in #62 , #66

Closed 2019-09-01.

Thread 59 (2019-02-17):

Fix Ethernet RJ45 footprint

npetersen2, 2019-02-17:
The REV C board doesn't have holes for the plastic alignment parts of the RJ45 Ethernet connector.

For assembly, we have cut off these plastic feet for every board. Please update the PCB footprint to add these holes so we don't have to do this.

npetersen2, 2019-04-19:
Fixed.

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

Closed 2019-04-19.

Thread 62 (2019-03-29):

Pick different low side switch MOSFETs for LED drivers

npetersen2, 2019-03-29:
The FPGA is driving 1.8V on the gate of the low side LED driver MOSFETs. This doesn't seem to be enough to fully activate the MOSFET as a switch, so the LEDs are very dim. I think we just need to find a different MOSFET with lower Vgs threshold...

npetersen2, 2019-09-01:
#66 Fixed, see other issue.

Closed 2019-09-01.

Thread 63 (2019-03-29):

Update BOM to include mechanical devices

npetersen2, 2019-03-29:
BOM should include the following:
- PicoZed heatsink
- PicoZed 100 pin connectors
- standoffs
- screws
- jumpers for headers

npetersen2, 2019-07-28:
Done: PicoZed connectors, standoffs, screws.

npetersen2, 2019-09-01:
Still need to add:
- jumpers for headers
- PicoZed heatsink

npetersen2, 2019-12-09:
Added PicoZed heatsink, now just need jumpers.

npetersen2, 2019-12-09:
Opted to just mark on silkscreen default locations for jumpers and add correct number to BOM.

Closed 2019-12-09.

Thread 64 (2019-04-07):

Replace PWM VDRIVE level shifters with different part

npetersen2, 2019-04-07:
The TC4468 part has been problematic for us. They keep breaking... See issue #44 for another example of problems.

This part is actually overspeced anyway. It is meant to drive significant current, but we are just translating logic signals. We just need a part that can do 5V to up to 15V. There are other parts to use.

Please fix this by removing TC4468 and replacing with something else.

npetersen2, 2019-12-09:
Looked into finding another part that has integrated AND gates for E-stop functionality... Couldn't find one...

Since the first month of REV A AMDC, this part hasn't broken, so I think that was a fluke. REV D will just continue using the same part.

Closed 2019-12-09.

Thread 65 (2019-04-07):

Use level-translation IC for UART signals

npetersen2, 2019-04-07:
The current design uses a MOSFET to translate between 1.8V to 3.3V for UART signals. Please replace this with a dedicated voltage translation IC.

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

npetersen2, 2019-07-28:
Done.

Closed 2019-07-28.

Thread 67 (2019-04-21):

Add VSUPPLY input terminal block for Powerstack power

npetersen2, 2019-04-21:
The Powerstack needs two power supplies (LV and HV). They should both come from the DB15 cable, and should be selectable on AMDC h/w.

LV: 1.8V, 3.3V, 5V
HV: 5V, VSUPPLY terminal block, VDRIVE terminal block

npetersen2, 2019-09-25:
Done, see updated requirements #78

Closed 2019-09-25.

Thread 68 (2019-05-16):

Analog input op amp failed

npetersen2, 2019-05-16:
Incident where U46 op-amp failed, causing a short between +15V and -15V. This brought down all the analog conditioning circuitry, as well as the attached current sensors as they used the same power rail.

See schematic below for which op-amp failed:
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

This op-amp is configured as unity gain to drive the sample and hold ADC. Note that during normal operation, these devices get warm (~40C). Perhaps this is due to the ADC sourcing current spikes many times per second (~900kHz). If one of these fails again, we will look into a design change.

elsevers, 2019-11-29:
@Nick-Hemenway Believes that this has now happened on three AMDCs

elsevers, 2019-11-29:
On the AMDC that @Anvar-Khamitov is debugging: the -15V rail is collapsed down to 0V (-15V_A is collapsed, -15V_B appears to be okay, as are all of the positive rails).

elsevers, 2019-11-29:
@ngadiyar93, @Anvar-Khamitov, and @mimayberry report that in a separate AMDC, a couple of the op amps get hot and the voltage rails occasionally collapse. Can one of you three can provide more information on this. Specifically, which power rails are collapsing (`-15V_A`, `-15V_B`, `+15V_A`, `+15V_B`)? Which op amps are getting hot?

elsevers, 2019-11-29:
This seems like something we need to debug. Let's come up with a plan.

One strategy: change the ADC sample rate down to a low value (like <10 kHz) or completely disable the ADC sampling and see if the issue goes away (for the AMDC where the power rails intermittently collapse). How hard is it to make the change? Does this require an update to verilog?

Anvar-Khamitov, 2019-12-02:
> On the AMDC that @Anvar-Khamitov is debugging: the -15V rail is collapsed down to 0V (`-15V_A` is collapsed, `-15V_B` appears to be okay, as are all of the positive rails).
>
> @Anvar-Khamitov, can you please reply to this with the serial number of this AMDC, so that we can keep the boards straight. Also, please add this issue to the board log for this AMDC.

Serial number is 05. The issue is added to the board log.

elsevers, 2019-12-02:
Please confirm that in all of these boards it is the `ADA4522` parts that are overheating/failing (not the INA2143` parts).

elsevers, 2019-12-02:
On the boards where the power rails intermittently collapse:
- what does the analog signal look like at the input and output of the `ADA4522` parts (when the rail is collapsed/is not collapsed)
- Erase the FPGA/DSP and confirm that the ADCs are not being sampled (verify that `ADC_CNV`, `ADC_SCK`, and `ADC_CLKOUT` are not active). Do the parts still get hot and do the voltage rails collapse?

Anvar-Khamitov, 2019-12-02:
> Please confirm that in all of these boards it is the `ADA4522` parts that are overheating/failing (not the `INA2143` parts).

@elsevers Based on the results using thermal camera, `ADA4522` parts are overheating, not `INA2143`. This can be seen in the image below for the board with the serial number 03: `ADA4522` are the ones with light yellow color, there are 4 of them. There are 2 `INA2143`-s under each `ADA4522`.
But we are not sure whether overheating of `ADA4522` means that it is failing, not `INA2143`.

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

Anvar-Khamitov, 2019-12-02:
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

@elsevers This board (serial number 03) has another issue. When connected to power supply, it starts beeping. According to @npetersen2 : "one of the DC/DC converters on the board is "hiccupping" ie it turns on, current limits, and turns itself off. This keeps repeating and is causing the beeping. This could mean either the power converters on AMDC are broken, or a component is broken, thus drawing way too much current from the DC/DC."

Due to this issue, I am not sure whether we can do tests with this board.

elsevers, 2019-12-03:
> @elsevers This board (serial number 03) has another issue. When connected to power supply, it starts beeping. According to @npetersen2 : "one of the DC/DC converters on the board is "hiccupping" ie it turns on, current limits, and turns itself off. This keeps repeating and is causing the beeping. This could mean either the power converters on AMDC are broken, or a component is broken, thus drawing way too much current from the DC/DC."
>
> Due to this issue, I am not sure whether we can do tests with this board.

I have created an issue #82 for you to track your debugging progress with the 5V supply / 2.048V reference problem with SN 03.

mimayberry, 2019-12-06:
The `-15V_A` rail on board 05 is now operational. The problem was an incorrectly placed voltage regulator. A +15V regulator was installed in place of the correct `-15V_A` regulator. The part in question is shown below:
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

elsevers, 2019-12-09:
Any update on who built this board? Was it Screaming Circuits?

mimayberry, 2019-12-09:
@elsevers The board log only says it was made by Beta.
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

elsevers, 2019-12-09:
Beta paid for Screaming Circuits to build those boards.

Anvar-Khamitov, 2019-12-23:
All 15 V voltage rails of AMDC with serial number 5 are collapsed: `-15V_A`, `-15V_B`, `+15V_A`, `+15V_B` are collapsed down to -1.84 V, -1.9 V, -0.93 V, -0.6 V, respectively. Started to debug this issue with @ASHAD1 . Possible cause might be ESD or AMDC overloading the op-amps.

ASHAD1, 2019-12-26:
The Analog conditioning circuitry of AMDC serial 5 failed again, we had replaced the ICs and its working now. These might be damaged because of ADC overloading (current spikes) the Op-amps as mentioned before in the previous comment, or this might happen because of ESD as mentioned by @Anvar-Khamitov

elsevers, 2019-12-27:
@ASHAD1 and @Anvar-Khamitov what parts did you have to replace? ADA4522 or the INA2143? And did you have to replace all of them or only certain ones?

My understanding is that these parts have not had to be replaced on this board previously (SN05). Is that correct?

ASHAD1, 2019-12-27:
@elsevers  we had replaced four INA2143 (U47C, U48C, U47D, U48D), all the ADA4522 opAmps and +15V regulators and -15V regulators.

These parts were not replaced previously on the board SN05.

elsevers, 2019-12-27:
@ASHAD1 Are you certain that all of these parts had failed? This is an important detail for debugging purposes: the INA2143 parts are not loaded by the ADCs (only the ADA4522 parts are) -- so if both have failed, this would seem to suggest either an ESD issue or some kind of systemic issue.

elsevers, 2019-12-28:
@ASHAD1 Has promised a write up with more debug information. It sounds like the ADA4522 parts failed initially and then the INA2143 parts failed during debugging.

@ASHAD1 and @Anvar-Khamitov: Do we have any evidence that the ADC’s sampling is causing the ADA4522's to warm up? Has anyone tried turning the ADC’s off and seeing if the ADA4522's cool off, then turning the ADC’s on and seeing if they warm back up? (This could be done by erasing the flash on the picozed and then using a probe to verify that the ADC’s are not active). *Can someone run this test on board SN05*... right away?

Further thoughts:
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
elsevers, 2019-12-29:
Thanks Anvar. What are the volts/div?

Any ideas what that small amount of noise is on the amplifier output when the picozed is unplugged?

Get Outlook for Android<https://aka.ms/ghei36>

________________________________
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

Anvar-Khamitov, 2019-12-29:
@elsevers  Below are some clearer plots. All these plots have 100 mV/div and 2 us/div (in the previous plots, it was 500 ns/div).

First photo shows ADA4522 voltage when picozed is plugged in. Second is when picozed is unplugged - it turns out that this noise is periodic. It seems to be ambient noise because this noise in the output of ADA4522 is still present even when there is no supply to the AMDC (third photo).

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

elsevers, 2019-12-30:
Thanks @Anvar-Khamitov. This was very helpful.

The ADA4522 is intended to operate as a unity gain amplifier. Its purpose was to give us a solid voltage source for the ADC to read from. However, it does not seem to be doing a great job of this, as evidenced in the plots above, and furthermore is periodically failing. We do not yet know why it is failing or why it is heating up (note that the part is in fact rated for infinite duration short circuit conditions.)

**I think we should consider removing the ADA4522/unity gain amplifier stage from Rev D.** This means that the output of the RC filter will connect directly through to the ADC pin. The ADC switches a 15 pF load in and out for each approximation (which seems to be causing the voltage spikes on the ADA4522 waveform). The RC filter is currently using a 33nF capacitor, which should certainly be stiff enough against the 15 pF load switching in and out.

It would be a good idea to validate that removing the ADA4522 results in working hardware before we make the change to Rev D. We can do this by removing the ADA4522 parts and soldering a jumper/short between the in+/in- pin pair of each amplifier (i.e., short pin 2 to pin 3; short pin 5 to pin 6; short pin 9 to pin 10; short pin 12 to pin 13).

- @Anvar-Khamitov and @ASHAD1 is this something you can test (_removing ADA4522s and adding shorts_) by the January 1st deadline that @npetersen2 has given us for board changes?

- I would like to see some LTSpice simulations validating the analog signal chain. I'll create this as a separate issue.

- Anyone have comments / feedback on my proposed change here?

Anvar-Khamitov, 2019-12-30:
I can try to test it today (removing ADA4522 parts).

npetersen2, 2019-12-30:
@Anvar-Khamitov @elsevers Were these tests performed with voltage applied to the input of the analog signal chain, or was it floating? I'm not sure how the system behaves when no input is connected.

@Anvar-Khamitov when you remove the ADA4522 part, can you try hooking up a reference input to the signal chain (maybe just constant 1V etc) and then probe that input plus any other signals of interest?

Anvar-Khamitov, 2019-12-30:
@npetersen2 There were no analog inputs, the voltage was floating when we performed these tests. Ideally, when there is 0 V input, ADA4522 output should be V_REF, but it was at around 2.059 V (mean of the voltage in the above pictures).

I can test with 1 V input after removing ADA4522.

Anvar-Khamitov, 2019-12-31:
@elsevers @npetersen2 After removing ADA4522s and adding shorts, it looks like there are no voltage spikes in the output signal due to ADC, as shown in the first photo (there is no input to the analog chain). Looks like it now has only ambient noise.

When 1 V is applied to the input of the analog chain, the output signal is shown in the second photo. Third photo shows the waveform of the input analog signal (1 V).

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

elsevers, 2019-12-31:
Thanks @Anvar-Khamitov. Very helpful to see these images. I am curious about that ~200 kHz noise that occurs when the AMDC is powered off...

I have proposed issue #88 to be implemented in REVD to address our problems here.

@Anvar-Khamitov, can you test this further by regulating closed loop currents when your analog signal chain is set up without the ADA4522 part?

Get Outlook for iOS<https://aka.ms/o0ukef>
________________________________
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

Anvar-Khamitov, 2019-12-31:
@elsevers I will be able to test it with closed loop current control on Thursday.

Anvar-Khamitov, 2020-01-02:
Here are some plots from the closed loop current regulation (no ADA4522 parts). I tested it for two cases.

Photo 1 shows reference and actual currents with reference current amplitude 1 A and frequency 50 Hz. Photo 2 is the output from INA2143 (input to ADC).

Photo 3 shows reference and actual currents with reference current amplitude 1.5 A and frequency 100 Hz. Photo 2 is the output from INA2143 (input to ADC).

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

Closed 2020-01-29.

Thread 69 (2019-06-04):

+/-15V LDO regulators for analog system not powerful enough

npetersen2, 2019-06-04:
When using 4x sensor cards plugged into the analog interface, the +/-15V power rails cannot support load.

@jjsylvestre can you please update this issue with more details?

npetersen2, 2019-09-25:
Decided to leave the +/-15V rails at 400mA max... If the application needs more, they have to source externally.

Closed 2019-09-25.

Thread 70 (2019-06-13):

Change encoder receiver IC

npetersen2, 2019-06-13:
From [recommendation at US Digital](https://www.usdigital.com/products/interfaces/encoder/cable-drivers/pc4), please replace encoder receiver IC with the mating pair to the one currently on the encoder.

http://www.ti.com/lit/ds/symlink/am26c32.pdf

Make sure to include terminate resistor for each input.

npetersen2, 2019-07-28:
Done.

Closed 2019-07-28.

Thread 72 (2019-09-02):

Add red/green LEDs for user I/O

npetersen2, 2019-09-02:
After working on the AMDC for an example application for Beta, I found that it would be REALLY nice to have a range of red / green LEDs to indicate status from code.

For example:
- G: no voltage command saturation, R: saturation
- G: no current command saturation, R: saturation
- G: sensorless position estimate is valid, R: not valid
etc

Please add a row of these LEDs which the user can control. For layout, space them such that the user can put little label stickers on the PCB for the ones they are using.

npetersen2, 2019-09-25:
Done.

Closed 2019-09-25.

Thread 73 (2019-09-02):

Remove user button and switches

npetersen2, 2019-09-02:
The REV C hardware has two piano switches for user input, as well as one push button.

Neither worked very well -- switches had many spurious changes of state, and button always reset entire board when pressed...? These switches can be emulated in software, either from the serial terminal interface or Ethernet interface.

Please remove them from design to reduce BOM and shrink PCB size.

npetersen2, 2019-09-02:
Done.

Closed 2019-09-02.

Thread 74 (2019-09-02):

Change analog supply rails to +/- 12V

npetersen2, 2019-09-02:
REV C hardware is designed to use +/- 15V voltage rails for the analog conditioning circuitry. We generate these by using (2) DC/DC (24V to 15V), and stacking them with middle being GND. We trim both away from GND to make about +/- 16V, then use LDOs to get clean +/- 15V.

Our input requirement is +/- 10V signals. We should use +/- 12V for analog circuitry! This lets us NOT trim our DC/DC converters (requires specific resistors not used anywhere else on board), and let's us use standard +/- 12V LDOs. This removes ~8 specific resistor values from the BOM and shrinks PCB.

Please remove trimming from 24V to 15V DC/DC converters, as well as change +/- 15V LDOs to +/- 12V LDOs. Update related schematic parts.

npetersen2, 2019-09-02:
Found some good looking LDOs to use:
- +12V: NCP1117DT12RKGOSCT-ND
- -12V: MC7912CD2TR4GOSCT-ND

npetersen2, 2019-09-02:
Also, probably up the DC/DC 24V to 15V converters to support 1A output (15W). See #69

npetersen2, 2019-09-25:
Decided to stick with +/-15V LDOs, and just switch to fixed versions to remove additional unique resistors. Seems to work well.

Closed 2019-09-25.

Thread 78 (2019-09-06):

Changes to PowerStack I/O cable

elsevers, 2019-09-06:
-Merge VDD / VIO to PowerStack: support 3.3V and 5V.
- Keep VDRIVE terminal connection as is
-Per discussion, add separate PSSUPPLY terminal that goes directly to DB15 connections. Each DB15 should have a high current 0 ohm resistor to let user select if power to powerstack comes from AMDC or not.

npetersen2, 2019-09-25:
Done.

Closed 2019-09-25.

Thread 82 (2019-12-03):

2.048V reference rails failed on AMDC Rev C SN03

elsevers, 2019-12-03:
I am creating an issue to track this.

AMDC Serial Number 03 has a problem where both of the 2.048V reference voltages are collapsed to nearly 0 V and one of the ADCs is burning hot. The 5.5V supply is beeping. If JP14 is removed, the beeping goes away.

Prior to this, @Anvar-Khamitov and @mimayberry observed that the 15V rails would randomly exhibit issue #68, but the op amps would recover. Is it possible that this is all some related systemic problem?

@Anvar-Khamitov and @mimayberry -- please use this issue to track your debugging status for this board.

mimayberry, 2019-12-04:
After removing the two 2.048V regulators, the 5V and 2.048V rails remain shorted to ground. The removed regulators appear to undamaged.
Without the regulators, the 5.5V supply continues to beep and the 5V rail drops to 4.7V.

mimayberry, 2019-12-06:
Removing both ADCs solved the beeping problem. Both components had internal shorts from `Vref` (2.048V) to ground.

For the +15V rail problem:
On analog channel A, removing both `ADA4522` parts had no effect on the `+15V_A` rails. Then, removing one `INA2143` IC brought `+15V_A` back to the correct voltage. This likely means the `INA2143` part went bad, although the cause is still unknown. The same procedure was repeated for channel B, now all of the +/-15V rails are operational on board 03.

Closed 2020-01-29.

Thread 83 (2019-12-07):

Adding over-voltage protection to the ADC input pins

ASHAD1, 2019-12-07:
ADC inputs are connected to op-amp which has a bias voltage of +15V and -15V, but the ADC inputs are rated for 8Vp-p.

npetersen2, 2019-12-09:
@ASHAD1 Do you have a part number recommendation on this? preferably something small, not BGA :)

npetersen2, 2019-12-15:
@ASHAD1 With new input protection (+/-19V), do we still need this?

ASHAD1, 2019-12-20:
@Nathan this protection should be fine. I also recommend changing the the Op-amp supply to single rail 0-5V.

elsevers, 2019-12-31:
If we implement #88, I think we can close this.

npetersen2, 2020-01-14:
Closed per #88 fixes.

Closed 2020-01-14.

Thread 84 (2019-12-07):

Adding 0 ohm resistor to the power line of the critical sections (like analog conditioning)

ASHAD1, 2019-12-07:
This will be useful for HW debugging, we can isolate each section from power by just removing the 0 ohm resistor.

npetersen2, 2019-12-09:
ADC voltage rails, analog +/-15V rails, and VREF supplies have been isolated with 0R resistors for REV D

Closed 2019-12-09.

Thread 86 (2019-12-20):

ADG3308 (encoder signal chain) has improper power rails on REV C

elsevers, 2019-12-20:
ADG3308 has improper power rails. The datasheet states that `VCCA` should always be less than `VCCY`, but on AMDC REVC `VCCA` is connected to 5V and `VCCY` is connected to 1.8V. This will cause problems.

Has this already been corrected for REVD?

elsevers, 2019-12-31:
@npetersen2 reports that this part will not be used on REVD. Can this issue be closed?

Anvar-Khamitov, 2020-01-02:
I checked whether I can directly connect MAX3097E (U5) to the picozed inputs by removing ADG3308 (U4) (REV C AMDC). Seems that I cannot do this because maximum input to picozed from the encoder chain is 2.35 V (VCCO + 0.55 V where VCCO = 1.8 V), while the output of MAX3097E is at around 3.5 V.

npetersen2, 2020-01-14:
This should be solved on REV D design. Will review at today's meeting, then close this issue.

Closed 2020-01-14.

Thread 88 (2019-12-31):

Revise analog signal chain: remove ADA4522 add high impedance resistor across inputs

elsevers, 2019-12-31:
In response to issue #68, please make the following changes:

- remove unity gain op amp stage (ADA4522)

- place a high impedance resistor across the analog input pins ANLG_P# to ANLG_N#. I suggest we try a 10k resistor

- revise input voltage protection circuitry (already completed)

elsevers, 2020-01-01:
Changing resistor to 100k as a precaution against a poor behaving sensor design

Closed 2020-01-14.

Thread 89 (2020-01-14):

Verify voltage rating of ADC protection

elsevers, 2020-01-14:
Verify that the +- 12V ADC input rating is compatible with:
- Kaman eddy current sensors (check part Nick just purchased as well as DIT 5200N)
- Current/voltage sensor board design

mimayberry, 2020-01-16:
The voltage output of the DIT 5200N is specified as +- 10V typical and the KD-2306 (Nick's) is
0-10V standard. The +-12V rating should be good for these sensors.

However the sensor boards are capable of outputting +-15V, therefore we may consider upgrading the TVS diode from the `SMDA12CTR` to the `SMDA15CTR` which has a reverse standoff of 15V. The reverse standoff voltage of a TVS should always be at or above the operating range of input circuitry.

Closed 2020-01-29.

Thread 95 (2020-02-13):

U12, U3 slightly wrong footprint

npetersen2, 2020-02-13:
Per Screaming Circuits -- U12, U3 have slightly too large footprint pitch. Please update footprint to match datasheet.

Note that this will probably be fine for REV D, perhaps minor rework will be needed. Part package is 0.65mm pitch while pad size is 0.95mm pitch. We might need to solder bridge the pads to the pins. Should be okay.

npetersen2, 2020-02-13:
Message from Screaming Circuits:

Issue 1 | Layout
-- | --
Part Description: | IC TRNSLTR BIDIRECTIONAL 6TSSOP
Part Number: | 1727-4560-1-ND
Mfg Part Number: | 74LVC1T45GW,125
RefDes: | U12,U3

```
Part package is SOT363 (2mm x 2.1mm: .65mm pitch)
Pad size is 2.5mm x 3.5mm: .95mm pitch.
Placing best fit. This issue is informational only. (FYI)
```

npetersen2, 2021-02-18:
1. Reviewed datasheet for device, determined the footprint on AMDC is wrong and does not match datasheet
2. Created new footprint entry in Library for the correct footprint per datasheet
3. Updated schematic lib entry to use new footprint
4. Replaced the parts on the schematics (U3, U12) with the new component to ensure new footprint will be used during PCB layout.

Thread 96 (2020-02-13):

Capacitors for analog input RC filter have wrong P/N in BOM

npetersen2, 2020-02-13:
Per Screaming Circuits --

The 33nF caps in the RC filters for the analog inputs are the wrong part number. The footprint is 0603, but the BOM is for a 1206 cap.

I have instructed Screaming Circuits to simply not populate anything for these caps. We can get the right parts and put them on ourselves.

npetersen2, 2020-02-13:
Message from Screaming Circuits:

Issue: 2 | Layout
-- | --
Part Description: | CAP CERM .033UF 10% 50V X7R 1206
Part Number: | 478-1548-1-ND
Mfg Part Number: | 12065C333KAT2A
RefDes: | C77A,C77B,C79A,C79B,C81A,C81B,C86A,C86B

```
Part package is 1206, pad size is 0603. How would you like us to proceed?
```

npetersen2, 2021-02-18:
1. Confirmed P/N in schematics (BOM) is for 1206 footprint, PCB is 0603.
2. Replaced P/N with 0603 device: https://www.digikey.com/en/products/detail/samsung-electro-mechanics/CL10B333KB8NNNC/3887699 (+/- 10%, 33nF, 0603, 50V rated)

Closed 2021-02-18.

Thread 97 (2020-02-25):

Add mechanical components to BOM for manufacturing

npetersen2, 2020-02-25:
On AMDC REV D, I created a schematic called "BackPage" which has models of screws, standoffs, heatsink, PicoZed connectors, jumpers, etc... These are the extra mechanical items needed for AMDC.

Turns out that if you generate the BOM while the PCB is the main document in Altium, it completely ignores items marked `Mechanical` for the BOM, but if you generate it from the schematics view, it includes them.... I did it from the PCB view, so all these mechanical items were not included in the BOM to Screaming Circuits.....

Please update BOM to include ALL components (i.e. generated from schematic view)...

npetersen2, 2020-02-25:
Note that I believe the needed parts are only on "BackPage" schematic doc:

| Qty | Digi-Key P/N | Comment | Designator | 11x Qty |
-- | -- | -- | -- | --
13 | KEY1046-ND | Screws | SCREW1..13 | 143
13 | 36-1656-ND | Standoffs | STANDOFF1..13 | 143
3 | 609-1693-1-ND | PicoZed Cons | CON16..18 | 33
1 | 1528-1697-ND | Heatsink | HEATSINK1 | 11
10 | S9337-ND | Jumpers | JMP1..10 | 110

npetersen2, 2021-02-26:
All required P/Ns are modeled in the `BackPage.SchDoc` sheet. Therefore, they will be included in the BOM when generated from the schematics view.

Closed 2021-02-26.

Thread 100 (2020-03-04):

JTAG USB data lines swapped

npetersen2, 2020-03-04:
The JTAG USB data lines (DATA_P and DATA_M) are swapped from the JTAG-SMT2-NC module to the micro USB connector CON9.

For REV D AMDC to function, the user must rework the board and swap these signals.

npetersen2, 2021-02-26:
Resolved via #158

Closed 2021-02-26.

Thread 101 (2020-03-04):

Switch to through-hole USB connectors

npetersen2, 2020-03-04:
The micro USB connectors are so fragile that they can easily rip off....

Switch to, at minimum, a through-hole micro USB connector. Strongly consider using USB Type B for JTAG / UART...

npetersen2, 2021-02-26:
Resolved via #158

Closed 2021-02-26.

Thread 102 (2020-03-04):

Add jumper for selecting external vs. default E-STOP and VDRIVE

npetersen2, 2020-03-04:
In the current REV D design, the PWM inverter interface will not function at all without wires plugged into the external screw connectors for `VDRIVE` and `ESTOP`.

Please add three-pin selectors for the following:

1. E-STOP: One position is external (functions like now), other position is enabled.
2. VDRIVE: One position is external (functions like now), other position is 5V.

npetersen2, 2021-02-25:
Added jumper for VDRIVE input:

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

Previously, VDRIVE connected straight to CON2 pin 1. Now, it goes through the header with the option of connecting board 5V directly, thus not needing to use the external pins.

npetersen2, 2021-02-25:
## E-STOP

### Before:

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

### After:

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

GnomeTek, 2021-03-21:
Approved

Closed 2021-02-25.

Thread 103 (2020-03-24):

isoSPI 24V power doesn't work

npetersen2, 2020-03-24:
The isoSPI connectors are supposed to have 24V power to supply the external circuitry if needed. Indeed, the `VIN2` signal is routed to pins at the connector, but there is an issue.

The `VIN2` is 24V, but in reference to the `VIN-` of the AMDC... NOT the common `GND`. This is due to the isolated DC/DC converters! Therefore, the 24V supply at the isoSPI connectors is NOT usable.

This may be okay since the 5V rail is still available for powering external boards.

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

npetersen2, 2021-02-08:
Per planning meeting, this issue should be solved. We want 24V available for the expansion port.

To solve, I propose adding another small isolated DC/DC, probably 6W rated is fine; 24V at 250mA:
https://www.digikey.com/en/products/detail/cui-inc/PQQ6W-Q24-S24-S/13402043

This would add ~$10 to BOM and take up board space, but I think it is worth it and an easy solution.

npetersen2, 2021-02-27:
Implemented:
1. Added 24V DC/DC to form isolated 24V rail
2. Used this new 24V rail for the GPIO port

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

GnomeTek, 2021-03-21:
Approved

Closed 2021-02-27.

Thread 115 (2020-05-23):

REV D BOM is missing standoffs and jumpers

elsevers, 2020-05-23:
The bill of materials is missing recommended:
1. standoffs (+ nuts)
1. jumpers (but header pins are included)
1. Picozed connectors (`JX1`, `JX2`, `JX3`)
1. Picozed

npetersen2, 2020-05-24:
@elsevers This issue already is documented here #97.

The PicoZed is not on the BOM since it cannot be bought from Digi-Key, while everything else can... I suppose another BOM file should be made for the different distribution companies (Digi-Key / Avnet)

npetersen2, 2021-02-26:
Resolved via #97

Closed 2021-02-26.

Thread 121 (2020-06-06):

Add pull-down resistor to VCCIO_EN

npetersen2, 2020-06-06:
Per @elsevers findings:

> Interestingly, one AMDC board actually has a 1.8V output from `U16` with no PicoZed installed. We don't have any pull down resistor on `LV_VCCIO_EN`. On most AMDCs, this floats around 0.3V and is interpretted by U12 as a logic low. On this one particular AMDC, LV_VCCIO_EN floats to ~1.1V and was interpretted by U12 as a logic high. I verified that there isn't a short in the JX2 connector, it just seems to be floating to this level due to the U12 internal impedance. Not sure if this matters, or if we should be considering a pull down resistor on a future rev of the AMDC.

I think we should add a 100k pull-down resistor to the `LV_VCCIO_EN` signal. This will put the AMDC into a known state when powered up with no PicoZed plugged in. Being in a known state will help users test the board (remove questions about what the state should be).

npetersen2, 2021-02-25:
Added 100k pull-down resistor:

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

Closed 2021-02-25.

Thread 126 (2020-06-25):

Add VDRIVE to DB15 connector for Power Stack interface

npetersen2, 2020-06-25:
Each DB15 connector for the Power Stack interface has the following signals:

Digital signals:
- 6x PWM outputs
- 4x status lines

Power:
- VDD
- VPS
- PSGND
- GND <== two pins are used for this!

We should remove one of the pins for GND and make it VDRIVE. There are some power stacks that need to know what VDRIVE is, so passing it in as a constant voltage input would be nice. We don't really need two GND pins anyway...

npetersen2, 2020-06-25:
Note that VDRIVE is referenced to GND, so using only 1 pin for VDRIVE is fine.

npetersen2, 2021-02-04:
Add a jumper or zero ohm resistor to disable this signal for compatibility.

npetersen2, 2021-02-25:
Original connector pin-out:

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

New pin-out:
No functional changes by default; pin 7 is still tied to GND. But, user can swap DNP 0R resistor to get pin 7 connected to VDRIVE if needed. Those are 1206 resistor footprints. Hopefully they'll fit on the PCB, otherwise, I'll go to 0603.

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

Closed 2021-02-25.

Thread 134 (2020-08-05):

Change DB15 connector part number

npetersen2, 2020-08-05:
On the REV D hardware, we are using 2x1 stacked high density DB15 connectors (sometimes called HD15). These work nice, but they don't have the screw posts built into them for securing cables.

Change the BOM to use the connector with the **screw lock**:

https://www.digikey.com/product-detail/en/norcomp-inc/178-H15-513R577/NOR1831-ND/9095327

npetersen2, 2021-02-25:
1. Created new footprint and schematic symbol for new P/N (footprint is the same but different STEP file which shows the screw locks).
2. Deleted CON10 and CON8 from schematics and replaced with new part.

Closed 2021-02-25.

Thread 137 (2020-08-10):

Fix board start-up PWM issues

npetersen2, 2020-08-10:
The Xilinx Zynq-7000 SoC is used to drive the PWM outputs on the AMDC. During start-up (and any time the FPGA has no bitstream loaded), I believe the pin outputs are random -- they float. This causes strange issues for PWM outputs...

I propose we change the hardware to default the PWM outputs to a known state when the FPGA is not actively driving them. This would usually require something like a pull down resistor on each output... The AMDC has 48 PWM outputs... that would be a lot of resistors!

However, the AMDC has hardware E-STOP support! When the E-STOP is activated, all PWM outputs go to the logic LOW state. This is exactly what we want during start-up. So, to implement this, we just need to AND the E-STOP signal with a digital output from the FPGA. There would just be one pull down on the output from the FPGA. This would cause all PWMs to start in a logic LOW state.

See this crude drawing, where the orange is the new hardware we need (AND gate and one pull-down resistor):

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

npetersen2, 2021-02-04:
Should be an OR in the orange logic gate

npetersen2, 2021-02-25:
I have implemented this:

1. Added pin-out from PicoZed called `LV_PS_DRIVE_EN`. When this pin is logic LOW, the drive should be disabled. Used PS_MIO44, which is a PS pin (i.e. connected to DSP, not FPGA). This saves us one pin from the FPGA since this pin won't toggle very fast, so having only DSP control of it is fine. I confirmed in the datasheets for the PicoZed that MIO Bank 1/501 is 1.8V logic, and PS_MIO[40-51] are on Bank 501, therefore, this pin is 1.8V logic.
2. Renamed old `DRIVE_EN` signal to be `ESTOP_DRIVE_EN` as it is 5V logic enable signal derived from ESTOP input.
3. Passed both `ESTOP_DRIVE_EN` and `LV_PS_DRIVE_EN` into `DriveInterface.SchDoc`
4. Added 1.8V to 5V level shift in `DriveInterface.SchDoc` for the `LV_PS_DRIVE_EN`
5. Added AND gate for `PS_DRIVE_EN` and `ESTOP_DRIVE_EN`
6. The final 5V logic `DRIVE_EN` signal then goes to all PWM drivers.

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

GnomeTek, 2021-03-22:
Circuit implemented as described. Approved!

Closed 2021-02-25.

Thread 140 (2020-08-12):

Rename "isoSPI" ports to "GPIO" ports

npetersen2, 2020-08-12:
The `isoSPI` subsystem should be called `GPIO` since it contains both SPI and diff I/O signals... This will prevent confusion.

Rename the subsystem in the schematics and PCB silkscreen labeling.

elsevers, 2020-08-13:
`GPIO` or `Expansion Port`?

npetersen2, 2021-02-26:
Closed with #141

Closed 2021-02-26.

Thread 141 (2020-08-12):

Remove isoSPI functionality from the GPIO ports

npetersen2, 2020-08-12:
This is a "large" decision, but I propose we completely remove isoSPI from the AMDC platform. isoSPI is great for low bandwidth communication (~1MHz SPI SCLK freq max), but for high-speed, real-time motor drives, this is not helpful. In fact, isoSPI is generally useless for us.

If we remove all isoSPI, we can then add two extra I/O to each GPIO expansion port; one diff input and one diff output. This would mean we have a 3-line I/O for each expansion port.

This would create compatibility issues with existing hardware, but I think this is the right approach. We can then stop changes the GPIO expansion port pin out.... I believe the only boards that would have to change are the DAC board and the SensorCard platform motherboard.

We should address this before REV E hardware design release.

@elsevers @ASHAD1

NOTE: If each GPIO port had 3 outputs and 3 inputs, then we could actually add two extra GPIO ports to the AMDC. This would mean we have four HD15 connectors (2 stacks of 2) for GPIO. Each HD15 port would have 3 inputs and 3 outputs. I think this is better than keeping isoSPI in the design.

npetersen2, 2021-02-26:
Implemented this issue:

1. Remove all isoSPI-related circuitry
2. Doubled the GPIO ports due to extra FPGA I/O available since SPI is no longer used

The isoSPI is now called GPIO. There are 2 stacks of 2 HD15 connectors, totaling 4 GPIO ports. Each port has 3 inputs and 3 outputs. All signals are differential. The signal naming is: `GPIO[1..4]_IN[1..3]` for inputs, `GPIO[1..4]_OUT[1..3]` for outputs.

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

psinha25, 2021-03-22:
@npetersen2 This looks good to me. Signals names (in terms of renaming) are correct. I also compared the provided schematic image above to the `uAMDC` schematics and things correct!

Closed 2021-02-26.

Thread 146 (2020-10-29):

DAC board: fix ESD protection

mimayberry, 2020-10-29:
The TVS diodes used for ESD protection keep the DAC from outputting correct voltages  when ±7.5 V outputs are commanded on each set of four channels.

The current TVS diode contains a center node, that allows for differential voltage to be applied the diodes. This leads to the diodes conducting and dropping the voltage at the DAC output. The current TVS diode looks like this:
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

Solution is to use a TVS diode without the center node. Like this:
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

npetersen2, 2022-02-24:
New part: https://www.digikey.com/en/products/detail/smc-diode-solutions/SMDA12CTR/6236252

codecubepi, 2022-04-12:
@npetersen2 I saw that you merged DAC REV C into develop. Can we close this issue now as well, since it was addressed in REV C? The linked PR didn't seem to auto-close it.

Closed 2022-04-19.

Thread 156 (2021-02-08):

Change shield termination 0R resistors to connect to VIN-, not the board GND layer

npetersen2, 2021-02-08:
Per discussion with @GnomeTek, we do not want the shield noise to be injected to the AMDC board common GND.

Instead, it should be shunted to the VIN ground. This can be accomplished by changing the connector termination resistors to connect to `VIN_GND` via a 1206 0R resistor and a thick trace width. Run the trace on the bottom layer and keep the resistors on the bottom layer as well.

Keep the default for these resistors as DNP.

npetersen2, 2021-02-27:
Implemented:
- Switch to 1206 footprints for resistors
- Keep resistors as DNP
- Change resistor termination from `GND` to `GND_IN`

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

GnomeTek, 2021-03-21:
With this being routed to the GND_In like you have now, I suggest placing the DNP as 0-Ohm so they are connected.

npetersen2, 2021-03-25:
Updated all shield termination to be 0R by default, not DNP.

See 95d763e78095244112f9fd5328cd76a998e2168f

Closed 2021-03-25.

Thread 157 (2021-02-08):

Add PTC resettable fuse inline with PWM outputs for short-circuit protection

npetersen2, 2021-02-08:
Per discussion with @GnomeTek, we should protect the PWM outputs from short-circuit / shoot-through currents. When the outputs of the PWM drivers short, it tends to cause the driver IC to fail.

Suggestion is to add a 0603 inline footprint to each PWM signal output line which should fit in the available board space.

The 0603 footprint will be populated by default with the $0.14 ea PTC resettable fuse: https://www.digikey.com/en/products/detail/bel-fuse-inc/0ZCM0004FF2G/10270530

Users can swap this out for a 0R resistor if they need more drive current, which is highly unlikely. The PTC resettable fuse supports up to ~100mA current and has a nominal resistance of 4 ohms. In nominal operating conditions, the output current is usually < 1mA...

npetersen2, 2021-02-25:
1. Created model of part and footprint.
2. Added inline to all PWM outputs:

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

GnomeTek, 2021-03-21:
Approved!

Closed 2021-02-25.

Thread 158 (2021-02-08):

Merge UART and JTAG into one interface using Digilent JTAG-SMT3-NC device

npetersen2, 2021-02-08:
The current hardware has two USB ports, one for UART and one for JTAG.

The JTAG module we are using has a new version which integrates the UART functionality, therefore only requiring one USB port. It exposes the UART interface to the host via a virtual COM port.

Please update the schematics and layout for this new interface, and delete all prior UART circuitry.

https://www.digikey.com/en/products/detail/digilent-inc/410-357-B/8605091

npetersen2, 2021-02-26:
Fairly major changes required to implement this issue:

1. Modeled two new P/Ns: `JTAG-SMT3-NC` and USB TYPE B receptacle
2. Created new schematic sheet which implements the USB connection to the JTAG-SMT3-NC device. It exports the JTAG and UART signals, plus a reset line.
3. Deleted the old JTAG sheet and UART sheet
4. Used the new sheet outputs to replace the old sheets (i.e. hooked the new sheet up to the PicoZed).

Overall, this simplifies the schematics, reduces part count by a lot, and provides a single host interface via USB for both JTAG and UART. Great!

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

npetersen2, 2021-02-26:
Definitely need reviews on this before ordering boards, but I'm confident in the design.

BrandtBuchda, 2021-03-19:
The `PS_SRST_B` seems to be missing a pull up resistor. Aside from that, it all looks correct according to the datasheets.

psinha25, 2021-03-22:
@npetersen2 I agree with @BrandtBuchda's comment above, everything looks correct based on the datasheet of the module. I believe on page 4 of the datasheet, there is a `10K` pull up resistor on the `PS_SRST_B` pin.

GnomeTek, 2021-03-22:
I agree w/ the others, looks good besides the pullup

npetersen2, 2021-03-25:
Reviewed datasheet per comments above and did the following:
1. Changed the series resistor by the reset button to be 100 ohms, down from 10k.
2. Reviewed PicoZed hardware design and found that no pull-up is included on the PicoZed for the `PS_SRST_B` signal
3. Determined that the pull-up voltage should be 1.8V
4. Add 10k pull-up to 1.8V on `PS_SRST_B` signal in the `JTAG_UART.SchDoc` sheet

Closed 2021-03-25.

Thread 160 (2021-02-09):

Add E-STOP logic signal as input to FPGA

npetersen2, 2021-02-09:
On the current hardware, when the user activates the E-STOP, all PWM outputs turn off (i.e. logic LOW). However, there is no indication of this event to the firmware. This creates a potentially scary situation if the e-stop is then unasserted and the control code was still running.

Please add a single pin input to the FPGA for the e-stop logic signal. This way, an interrupt can occur in the firmware so the user can take action!

npetersen2, 2021-02-25:
1. Added 5V to 1.8V level shifter from the `ESTOP_DRIVE_EN` to `LV_ESTOP_DRIVE_EN` signal
2. Connected `LV_ESTOP_DRIVE_EN` to PS_MIO49
3. Confirmed PS_MIO49 is 1.8V logic
4. Confirmed we can enable interrupts on PS_MIO49 to detect ESTOP button press

GnomeTek, 2021-03-21:
Approved!

*did not track down #4 confirming ISR capable input.

psinha25, 2021-03-22:
Looks good to me @npetersen2

Closed 2021-02-25.

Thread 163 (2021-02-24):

Power Protection Circuit Modifications

GnomeTek, 2021-02-24:
These updates will allow proper operation of the input protection circuit.

Update resistance values
- R83 - 0 Ohm/ Remove
- R55 - 390K ohm
- R58 - 4.12K ohm
- R59 - 5.9K ohm

Add filter capacitors (surface mount ceramic works fine)
- 56nF from OV pin to GND
- 56nF from UV pin to GND

Add pullup resistor from !FAULT to VIN for debugging. Fault is a pull down only.
- 100K Ohm

npetersen2, 2021-02-25:
Implemented the required changes. I used 100nF filter caps, hopefully that is ok, @GnomeTek?

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

@GnomeTek can you provide the equations you used to compute the resistor values? Or the script, etc. I would like to update the note in the schematics:

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

If at all possible, I would love construct the resistance values from just a few 10k and 100k P/Ns that are already in the BOM. Could do 2 10k in parallel to get ~5k. Then, 4 100k in series to get ~400k. Could replace the SHDN pullup with 2 100k. This would remove ~4 lines from the BOM! @GnomeTek thoughts?

npetersen2, 2021-02-25:
Updated filter caps to 33nF per @GnomeTek comments.

npetersen2, 2021-02-26:
Script from @GnomeTek for computing resistor values:

```MATLAB
clc;
close all;
clear all;

%% AMDC Curr Vals
R3 = 11.8e6;        % R55 & R83 = 5.9Meg each 11.8Meg
R2 = 121e3;         % R58 = 121K
R1 = 178e3;         % R59 178K
%% Figure voltages from resistors
Iuv = 10e-9;        %abs minimum 10nA
Vos_UV = Iuv*(R1+R2);    % max tolerable offset of UV% 3mV
Ruv = Vos_UV/Iuv;
UVth = R3*.5/Ruv+.5;      % 20.232 v
OVth = 0.5*(Ruv+R3)/R1;     %33.986 v

%% Procedure for figuring resistors
Iuv = 10e-7;        % [A] abs minimum 10nA  % 1 pick bias current
Vos_UV = 10e-3;     % [V] choose UV offset tolerance
UVth = 20.;         % [V] Under voltage threshold
OVth = 34;          % [V] Over voltage threshold
Ruv = Vos_UV/Iuv;
R3 = Ruv*(UVth - 0.5)/0.5;   % [Ohm]
R1 = ((Ruv+R3)/OVth)*0.5;    % [Ohm]
R2 = Ruv-R1;                 % [Ohm]
Itotal = OVth/(R3+R2+R1);    % [A]
P_R3 = Itotal^2*R3;          % [W]
P_R2 = Itotal^2*R2;          % [W]
P_R1 = Itotal^2*R1;          % [W]
```

GnomeTek, 2021-03-21:
Approved!

Closed 2021-02-26.

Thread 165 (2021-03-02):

Add extra capacitor and pull-up resistor near the reset switch to reduce resetting due to ESD.

ASHAD1, 2021-03-02:
I would also prefer to have a TVS diode near the switch.
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

GnomeTek, 2021-03-04:
Thinking about this, I think @ASHAD1 suggestion of having a TVS is a great idea, my comments were to be added along with that.
In summary:
TVS near the switch to inline resistor (10k? pick a nice common value you have) and the 100nF that is in place is adequate.

npetersen2, 2021-03-17:
@ASHAD1 @GnomeTek I think I've added what you both have recommended:

Please review.

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

GnomeTek, 2021-03-17:
This will work, although best practice is to place TVS as close as possible to external source. So close to SW1, on the other side of R21.

npetersen2, 2021-03-25:
Rearranged ordering of components per above comments.

See 332976bfcc88670f4fcbdf6df80678a233aa8aa7

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

Closed 2021-03-25.

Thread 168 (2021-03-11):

AMDC restart issue

elsevers, 2021-03-11:
This issue is documenting observation of an EMI issue in the AMDC REV D. In this instance, the USB UART link to the PC would itself, presumably due to EMI.

- The problem occurs when a command is issued to enable the PWM interface while two 3phase inverters are connected to the PWM ports with the DC link energized. If the DC link is at a "low" voltage, this issue never appeared (in this case, low voltage was 30V; a 50V bus caused the issue quite repeatably)

- When the PWM interface enable command would go out, the AMDC would stop responding to UART commands from the PC. However, **it did not restart itself**. The AMDC was still alive (@ASHAD1, can you confirm that the AMDC was still executing code properly? was there a heartbeat LED blinking?), but we could not communicate with it via UART.

- To get the AMDC to communicate via UART again we restarted the AMDC and disconnected/reconnected the USB cable to the PC. We would restart the AMDC by pressing the restart button on the board. We did not have to cycle power on the AMDC.

- We were using a laptop and disconnected the laptop's power supply so that the laptop had no earth ground in it. This did not in any way change the problem. This fact, combined with the restart of the AMDC fixing the communications, leads me to conclude that it is AMDC hardware that is ceasing to function properly.

- When the PWM interface enable command went out, *I think* (@ASHAD1 please edit this text to make it correct) that all PWM duty ratios were set to a value that should cause no current to flow in the three phase inverter but that the inverter would start switching at this point. For example, maybe they were all set to 50%.

*Brain storming on causes/solutions:* Perhaps this indicates that the current USB UART IC is overly sensitive to noise, and this problem will be resolved in REV E by usage of the new part. Alternatively, I am wondering if this issue makes a case for adding some sort of EMI protection on the PWM ports. OR, perhaps this makes the case for moving the AMDC further away from power stacks / current carrying conductors and into an EMI shielded box...

ASHAD1, 2021-03-11:
@elsevers the issue that you have described is correct, this happened before when I was testing the BP1 motor. When PWM is turned on (all duty ratio set to 50%) the UART link is disconnected, but the AMDC doesn't restart -- I can see that LED indicating PWM status was still on after the EMI event.
The event occurs at higher bus-voltage. I have noticed for bp1 this occurred at 100V bus voltage, for bless IM (Jiahao prototype) this occurred at 50V bus voltage.

npetersen2, 2022-04-19:
I am closing this issue as it has not been a problem with anyone recently, please reopen if any concerns come up.

Closed 2022-04-19.

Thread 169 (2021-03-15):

Connect mounting holes to chassis GND, not the isolated board common

npetersen2, 2021-03-15:
All mounting holes are current connected to `GND` -- the AMDC common ground (i.e. ground plane).

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

If the AMDC is screwed to a metallic box with metal stand-offs (as in the BOM), this will connect the board common to the outer world... This should be avoided.

Fix this by connecting the mounting holes to `GND_IN` -- i.e. the input supply voltage source which exists BEFORE the power input stage and isolation etc.

npetersen2, 2021-03-17:
Updated all mounting holes to `GND_IN`

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

GnomeTek, 2021-03-21:
Approved!

Closed 2021-03-17.

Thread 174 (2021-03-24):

Power Stack Supply Voltage Designations

GnomeTek, 2021-03-24:
Power Stack Power Supply is noted differently in different places. The biggest offender is page 1 of schematic it's referenced as VDDPS. This is what prompted the deep dive for me.

Power Stack Supply Voltage (Not PWM drive voltage)
- VINPS - on silkscreen
- VDDPS - on schematic block diagram (1st page)
- VIN_PS - Noted in PowerDistribution.md under Power Stack heading
- VPS in powerstack.md
- Not present in Power.schDoc
- **VIN_PS net label**

Suggest:

- Update schematic 1st page block diagram
      VDDPS -> VINPS  (To match silkscreen)
- Update all text references, including block diagram in PowerStack.md
      VPS -> VINPS
- Include VINPS and any other pass through/externally supplied power in PowerDistribution.md Block Diagram
- Move "Power Connections" from BoardIO to Power schematic (or link them via schematic ports. Absolutely valid to have them listed on BoardIO. but also needs to be noted on Power, even as a pass through)

Reference from VINPS to VIN_PS is trivial for a person to make. No need to update schematic net names or silkscreens. IMO.

npetersen2, 2021-03-25:
Implemented the following:
1. Changed block diagram label from `VDDPS` to `VINPS` -- this was a mistake
2. Updated `BoardIO` sheet to expose power signals as ports, and implemented connectivity in the `Power` sheet to make schematics easier to read.

Did not update the GitHub markdown docs -- we'll need to create a separate issue for this.

npetersen2, 2021-03-25:
Closing. See new issue #176 for continuation.

Closed 2021-03-25.

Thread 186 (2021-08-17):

System will intermittently fail to properly boot from EEprom

GnomeTek, 2021-08-17:
System will intermittently fail to properly boot from EEprom, causing several power cycle to get to "catch"

Hunch says setup and hold times are being violated after power cycle between the FPGA and the EEprom chip. Likely the EEprom takes longer to initialize to a ready state then the FPGA. The FPGA then initiates communication when the EEprom is not ready, and FPGA fails to load bitsream.

npetersen2, 2021-08-18:
I agree with this, however, the interface between the fpga and the memory chip is entirely managed on the PicoZed device. Therefore, I think it will be hard for us to adjust the interface to meet the required timing.

As a first step, I propose we should simply lower the clock frequency used to retrieve the bitstream from the memory device. Also, we can insert timing delays into the bootloader image on the processing system to try to wait for the memory to warm up.

GnomeTek, 2021-08-18:
Oh good, we have some options for control from the FPGA. I was worried there would be none since the system is in a cold boot state.
Let me get a scope on it and verify that is the issue at hand. I need to deploy my controller to EEprom first. Other tasks are higher priority at the moment.

npetersen2, 2022-04-19:
@GnomeTek I believe this issue to be resolved on the REV E hardware design, so I am closing. Please reopen if you find it still problematic.

Closed 2022-04-19.

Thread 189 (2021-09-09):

Change SCREW1..13 P/N in BOM and Altium

npetersen2, 2021-09-09:
Per a mix up with REV E assembly, change the P/N for SCREW1..13 to be: `36-9900-ND`

npetersen2, 2023-09-29:
Confirmed that REV F changes in PR #228 resolved this issue.

codecubepi, 2023-10-04:
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

Approved! It looks like all screws have the correct supplier part number.

npetersen2, 2024-03-27:
Closing since this was resolved in the REV F hardware

Closed 2024-03-27.

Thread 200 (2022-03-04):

DAC board: update connector interface to AMDC

npetersen2, 2022-03-04:
This issue supersedes #143 -- resolving this issue will fix #143

---

The REV B hardware design for the DAC board is designed so that the DAC can be used with either:

- GPIO expansion port (in REV B design, this is referred to as "IsoSPI")
- Power stack port

The REV C hardware design that @codecubepi and @wknutson are working on requires changes to this AMDC interface.

## Required Changes

The REV C DAC is still expected to work with both the GPIO expansion port and the power stack port. However, the hardware interface is now only supporting the latest AMDC hardware, REV E. On AMDC REV E, the GPIO port interface has changed. These changes need to be incorporated into the new DAC board design.

Specifically, the DAC board will no longer have any "isoSPI" hardware on it. All the isoSPI related devices should be deleted.

### AMDC interface

The DAC requires 3 logic wires for the AMDC interface: `CS`, `SCLK` and `SDI` -- these form the SPI interface. For the actual DAC IC, these signals are single-ended and range from 0V to 5V. These 3 signals need to come from the AMDC.

When plugged into the power stack port, the power stack status lines are used for the 3 signals. These status line signals from the AMDC are also single-ended. Therefore, they are directly compatible with the DAC IC.

When plugged into the GPIO expansion port, the 3 output signals are used for the SPI. However, these signals from the AMDC are differential. This means that the DAC board will need a differential-to-single ended converter for this interface.

For both interfaces, the goal of the DAC board is to be isolated from the AMDC. To do this, an isolator is used. See `U1` in the REV B DAC board design. This isolator will remain in the REV C DAC design.

Closed 2022-04-12.

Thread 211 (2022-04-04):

AMDC: Fix footprint TSOP65P640X120-16N for AM26C32 Sig-Diff

codecubepi, 2022-04-04:
While working on the DAC Board Rev C, I found that the footprint for the AM26C32 (TSOP65P640X120-16N in PcbLib) did not pass the DRC. Two issues:

- The outline silkscreen was too close to the pads. Move the outline X to +/- 1.6mm.

- The Solder Mask Expansion on the pads was too wide. Set Solder Mask Expansion on all pads to Manual, 0.04mm.

npetersen2, 2022-04-05:
Thanks @codecubepi for flagging this! We'll keep this on the back burner for the next version of the AMDC hardware

codecubepi, 2023-10-04:
Approved!

npetersen2, 2024-03-27:
Closing since this was resolved in the REV F hardware

Closed 2024-03-27.

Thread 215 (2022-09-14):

IC Failure Issue: AMDC Rev E, AM26C31 transciever on expansion port failure

Zhouzhou377, 2022-09-14:
## Problem
Two AMDC users have reported a failure with the AM26C31 IC, the differential output transceiver that drives the four expansion ports. In both cases:
- U46 failed
- The board connected to the expansion port was a [REV B Kaman IO Converter Board](https://github.com/Severson-Group/AMDC-Hardware/tree/develop/Accessories/Kaman_IO_ConverterBoard/REV20210414B).

One user also reported that their Kaman IO Converter Board stopped working at the same time that this IC failed.

One user replaced U46 in their AMDC and the expansion port began working again.

## Possible Cause
Note that the Kaman IO Converter Board Rev B does not provide any termination resistor for the differential signal:
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
The data sheet for the receiver part indicates that a termination resistor should be provided.

Upon inspection with an oscilloscope, large voltage overshoots are observed at the AM26C31 pins. We are speculating that the AM26C31 part may have become damaged by voltage reflections from the non-terminated expansion board.

npetersen2, 2023-09-05:
The Kaman expander board was updated in REV C (https://github.com/Severson-Group/AMDC-Hardware/pull/225) to include the termination resistors discussed in this issue.

Per the new REV C Kaman board updates, I am marking this issue as "solved" and closing it.

Closed 2023-09-05.

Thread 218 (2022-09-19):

Kaman I/O Board: Add diff I/O termination resistors

npetersen2, 2022-09-19:
## Issue Description

The I/O between the AMDC and the Kaman adapter board is differential. However, there is no termination resistors on the signals, either on the AMDC or the Kaman adapter board. This causes ringing and voltage overshoots. The datasheet highly recommends a termination resistor of 80-120 ohms.

## Changes Requested

Add four termination resistors to the Kaman adapter board design. Attach between the `_P` and `_N` signals:

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

## Hardware Testing Results

Here are a few scope captures of the original board with no termination resistors, and then with added termination resistors of ~120 ohms. All captures are the raw diff I/O, so you will see a nominal polarity and the negated polarity.

In the captures below, `C8` is always the filtered `CNV_n` signal to the Kaman sensors. The `CNV_n` falling edge triggers the ADC sampling.

### 1. `CNV_n` signal

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

### 2. `SCK` signal

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

### 3. `CNV_n` signal, with termination resistor

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

### 4. `SCK` signal, with termination resistor

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

elsevers, 2023-01-18:
Thanks @npetersen2. I am noticing that the voltage levels in these signals appear to be at ~3.3V level. I am confused by this because the transceivers on both the AMDC (i.e. U46) and the adapter board are at 5V. Shouldn't we expect to see these signals go between 0V and 5V?

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

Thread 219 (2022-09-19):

Kaman I/O Board: failed Schmitt trigger IC used for glitch filter

npetersen2, 2022-09-19:
## Description

On one of the Kaman adapter boards in the lab, I found that the second stage Schmitt trigger IC had failed.

Adding this issue so others have an idea of what to look for, should they run into issues.

## Hardware Waveforms

The glitch filter on the Kaman adapter board is composed of two Schmitt triggers and two RC LPFs. The filters help remove high frequency glitches and the Schmitt triggers convert the "soft" filtered waveform back to being a sharp square wave.

The waveforms below are captured on a board where the RC LPFs were altered to be `R = 10 kOhm` and `C = 1 pF` for both filters. This results in a higher bandwidth for the second filter.

I scoped the signal chain for the `SCK` line with no external noise (i.e. no DC link PWM switching)

### 1. Input from diff I/O receiver

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

### 2. First RC filter output

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

### 3. Output of 1st Schmitt trigger

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

### 4. Second RC filter output

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

### 5. Output of 2nd Schmitt trigger

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

**Notice the bad waveform from the second Schmitt trigger!!**

It appears the output stage low-side driver is damaged--there are sharp rising edges, but "RC" falling edges.

After replacing the 2nd Schmitt trigger with a different IC, the output became square wave again.

codecubepi, 2023-05-19:
I am experiencing a similar issue, my second Schmitt trigger IC seems to be faulty and lose the SCLK line entirely

#### Input to first Schmitt Trigger

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

#### Output of second Schmitt Trigger

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

npetersen2, 2023-09-28:
@codecubepi I am trying to remember what this issue is...

How does the firmware updates fix the hardware issue? I think this is related to a termination resistor (?)

codecubepi, 2023-09-28:
I think there were two related hardware issues here:

1. The trigger ICs used on that board occasionally go faulty, which we just just fixed by replacing them (I know I had to replace the IC at least once). I think that was the issue you encountered, which I guess would not be fixed by firmware, only be replacing the part.
2. The issue I mentioned was that the filtering was too aggressive for the higher SCLK frequencies we were running at in May. We fixed that by changing the RC values on the REV C Kaman Adapter board, and then making the filter delay configurable in the firmware.

npetersen2, 2023-10-08:
@codecubepi thanks.

Let's close this issue for now and re-open or create a new one if/when someone runs into a similar issue down the road.

elsevers, 2024-04-30:
@anirudhupadhyaya has created issue #231 which seems to be documenting the same problem. He addressed it by soldering in new components. You'll notice in the pictures of his adapters board that he has a large number of fly wires soldered in. The current theory is that these wires picked up ESD which damaged the Schmitt triggers. At this point, we aren't planning any design changes in response.

Closed 2023-10-08.

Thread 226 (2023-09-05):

AMDC: No termination on incoming GPIO signals

npetersen2, 2023-09-05:
After reviewing the GPIO interface per #215, @DivyaMendpara and I found that the AMDC has no termination on the input signals for GPIO... the datasheets for the Rx and Tx drivers (https://www.ti.com/lit/ds/symlink/am26c31.pdf, https://www.ti.com/lit/ds/symlink/am26c32.pdf) say there should be termination on the receiver side, not the transmit side.

Therefore, we need to add termination to the AMDC for the incoming GPIO signals.

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

There are 12 total input diff pairs, meaning 12 termination resistors should be added.

To save space, Nathan recommends using a SMD resistor array, for example: https://www.digikey.com/short/mtw2d204

The size of the package should be determined based on power rating... This is probably small, so something like 0603 is fine... You'll need to translate this into the array size.. i.e., each of the 4 in the array would be 0603, so Digi-Key will tell you the total size, not the per-resistor size... 0603 resistor has 63 mW rating, and it looks like a 1206 4-array resistor has 63 mW per element. So, let's go with 1206 size 4-array.

npetersen2, 2023-09-29:
I validated the schematic changes and PCB change. The routing to get the termination resistors into the design was a bit hairy...

I reworked it a bit, making use of an internal signal layer to try and get it cleaner and more logical.

codecubepi, 2023-10-04:
@DivyaMendpara @npetersen2

Questions on the routing (copied from my reply on #228 ):

Is there a reason this trace for GPIO4_IN3_P wraps around the via? Is this a length-match? If it's not, I think we could take the trace directly to the via (like the dashed red line). If it is a length-match, disregard.
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

Why is there a trace loop on GPIO1_IN2_N?
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

npetersen2, 2024-03-27:
Closing since this was resolved in the REV F hardware

Closed 2024-03-27.

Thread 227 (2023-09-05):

AMDC: PWM gate signals invalid during boot-up

npetersen2, 2023-09-05:
Many (all) users of the AMDC have reported that, during boot-up, their inverter power stacks have a shoot-through event. This typically causes the user's DC link power supply to go into current limiting mode.

~~I believe the root cause of this is the FPGA output pins go into high-Z state when no bitstream is loaded. Since PWM gate signals coming out of the AMDC are driven by the FPGA pins. The 1.8V logic level output from the FPGA is level translated twice: 1.8V to 5V, then 5V to `VDRIVE`. I believe the first voltage translation (1.8V to 5V) ends up latching in the "high-Z" state, which means the final gate signal is indeterminate and often leads to shorting the inverter half bridge.~~

Before we try to fix this, we need to understand exactly what is causing this issue...

It looks like this circuitry below should be protecting us from any issues during boot-up:

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

It looks like the pull-down resistor `R97` should be ensuring `DRIVE_EN` is always `LOW` during boot, i.e., when `LV_PS_DRIVE_EN` is not defined. Since all the PWM gate signal outputs are enabled/disabled by `DRIVE_EN`, this signal pull-down resistor `R97` should disable everything... But, it seems this is not working....

Let's get a REV E AMDC board and probe this signal chain during boot to see what actually happens! Why doesn't this work?

Potential idea why: `LV_PS_DRIVE_EN` is actually being driven `HIGH` during boot,.... then, our pull-down `R97` wouldn't be effective... Let's probe the top side of `R97` (i.e., pin 3 on `U42`) and see if it is high or low during boot.

npetersen2, 2023-09-14:
Good debugging session with @DivyaMendpara. We determined the root of the issue.

## Testing

During boot-up, we probed the signal path seen below:

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

We found that node `B` was 5V, and since `ESTOP_DRIVE_EN` was high, this means that node `C` was also high. This results in the PWM gate signal outputs on the AMDC to be active...and thus can result in undefined behavior during boot-up since the FPGA pins are high-Z.

The root cause is that node `A` was measured to be 1V during boot-up. After the PS starts running, node `A` drops to 0V. Then, when the PWM output is enabled, node `A` goes to 1.8V (as expected). However, when the AMDC is reprogrammed, node `A` is a steady 1V.

## Problem

The issue is that the pull-down `R97` is not strong enough... Based on simple math, it looks like a high-Z PS pin on the board we tested seems to source about 0.1 mA, which, driving through 10k resistor, is 1V. This tricks `U42` into thinking its input is high, which causes the whole issue.

## Solution

We need node `A` to remain low (close to 0V) when 0.1 mA is pushed into it... thus, we can change R97 to 10x smaller resistance to have a stronger pull-down.

We tested this on hardware by replacing R97 with a 1kOhm resistor. As expected, node `A` voltage during boot-up was reduced to about 120 mV. This is below the "high" threshold of U42, so nodes `B` and `C` remained low! We confirmed that the PWM outputs remained low during boot-up. Problem solved!

### TLDR Solution

Change `R97` from 10kOhm to 1kOhm.

npetersen2, 2023-09-18:
The REV E BOM does not have a 1k 0603 resistor already... but it has 470 ohm 0603.

Let's use 2x 470 ohms in series for this pull-down.

npetersen2, 2023-09-29:
I checked the schematic and PCB changes around this issue---looks good!

The schematic value text was not quite in the "right place," so I had Altium replace it to be the default spot. This was a super minor change which I committed to the branch.

codecubepi, 2023-10-04:
Approved!

npetersen2, 2024-03-27:
Closing since this was resolved in the REV F hardware

Closed 2024-03-27.

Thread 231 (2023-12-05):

U3B and U7 failure in Kaman adapter board during testing

anirudhupadhyaya, 2023-12-05:
# Context

In the ARL project for BP4 drive, we are using two Kaman eddy current sensors. During Anirudh's testing one of the Kaman demodulator boxes got  damaged, more details on this in Severson-Group/ARL-eturbo#37. When trying to re-configure the eddy current sensors it was found that the two Kaman adapter boards had also suffered some damage. It is unclear the sequence of events or cause/ effect relationship right now.

# Details

## Board 1
Schmitt trigger IC U3B was found to be damaged. Hence the SCLK and CNV signals to the demodulator is not correct, so no data is received.

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

### Scope captures

I and @npetersen2 probed the CNV and SCLK signals at three locations marked 1,2 and 3. The signals at 1 and 2 look as expected while the signals at 3 at the output of U3B does not look good.

_**SCLK at 1**_

This is the clock signal from AMDC after level shifting. CLK frequency - 2000 kHz. Looks good.

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

_**SCLK at 2**_

This should be inverted of 1 and thats what we see.

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.

_**SCLK at 3**_

This signal is not as expected. Does not look like a good CLK signal.
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

_**CNV at 1**_
Looks good.
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

_**CNV at _2_**_
Should be inverted from 1. Looks good.
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

**_CNV at 3_**

Not looking good here. RC behavior seen, instead of a square pulse.

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

## Board 2

In this board we found that IC U7 was damaged. This is responsible for level shifting the SCLK and CNV signals from the AMDC.
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

### Scope capture
SCLK signal at output of U7. Not looking good. This is not as expected, hence led us to the conclusion that U7 is damaged.

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

### Additional point
However, Anirudh found that after fixing this part the board was not working as expected. Further debugging revealed that U3B also to be damaged like board 1.

elsevers, 2024-03-26:
**Outcome:** @anirudhupadhyaya was able to repair both boards and them working for his purposes by replacing the components described above.

@anirudhupadhyaya or @npetersen2, can one of you leave a comment on if this issue should motivate any changes to the adapter board design?

anirudhupadhyaya, 2024-04-30:
Per my understanding here, U3A and U3B (second schmitt trigger IC) have been damaged on several boards during testing apart from this instance.. There could be some benefit to investigating this failure further and identifying a better IC

Closed 2024-04-30.

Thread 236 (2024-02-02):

TestBoard: find alternative part for BNC connector

npetersen2, 2024-02-02:
The BNC connector (https://www.digikey.com/en/products/detail/te-connectivity-amp-connectors/5-1634503-1/1755969) in the BOM for the AMDC TestBoard is obsolete. We need to find a replacement.

It should be footprint compatible with the existing part.

@codecubepi when you get a chance, can you please look for one and post a reply to this issue with suitable options?

codecubepi, 2024-02-06:
@npetersen2

## *Original Part:* TE Connectivity 5-1634503-1 [DigiKey](https://www.digikey.com/en/products/detail/te-connectivity-amp-connectors/5-1634503-1/1755969) [Mfg](https://www.te.com/usa-en/product-5-1634503-1.html)

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

- [x] Height from PCB 13.7mm

## *DigiKey Recommended Alternate:* Amphenol 112404 [DigiKey](https://www.digikey.com/en/products/detail/amphenol-rf/112404/1011728)

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

- [x] Should be *close enough* to be footprint-compatible
- [x] Height from PCB also 13.7mm
- [x] DigiKey lists same key specs: 50 ohm impedance, 4 GHz max freq, 500 V
- [x] DigiKey In-Stock (and Normally Stocking), Unit Price 3.68 USD

## *TE Conn. Recommended Replacement*: TE Connectivity 5413969-2 [DigiKey](https://www.digikey.com/en/products/detail/te-connectivity-amp-connectors/5413969-2/2188140) [Mfg](https://www.te.com/usa-en/product-5413969-2.html)

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

- [ ] This is not even as close as the Amphenol above to being footprint-compatible
- [ ] The connector height is also much taller, 20.57mm from PCB
- [x] Same key specs: 50 ohm impedance, 4 GHz max freq, 500 V
- [x] DigiKey In-Stock (and Normally Stocking), Unit Price 5.02 USD

## *My Alternate Pick*: Cinch Connectivity VB335 [DigiKey](https://www.digikey.com/en/products/detail/cinch-connectivity-solutions/VB335/4430332)

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

- [x] Close enough to be footprint-compatible
- [ ] Height from PCB 18.7mm
- [x] Same key specs
- [x] DigiKey In-Stock (and Normally Stocking), Unit Price 4.14 USD

codecubepi, 2024-02-06:
If I were to choose from those three alternates, I'd probably go with the Amphenol alternate recommended by DigiKey.

Closed 2024-02-13.

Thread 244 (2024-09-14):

DAC Board: Incorrect Pinout on U9 Linear Regulator

codecubepi, 2024-09-14:
On the DAC REV B, component U9 (a -15V/-12V linear regulator) has an incorrect schematic symbol and footprint. The datasheet specifies that this component has the following pinout:

- Pin 1: GND
- Pin 2/4: Input (-15V)
- Pin 3: Output (-12V)

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

However, this is the schematic symbol used in the REV B design:

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

Pins 1 and 4 need to be swapped, as the pinout of the negative voltage linear regulator is not the same as that of the positive linear regulator (U8, datasheet [here](https://www.onsemi.com/pdf/datasheet/mc78m00-d.pdf)).

It looks like this issue was solved via a rework on the DAC REV B:

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

*However, the issue was never documented*, and thus has persisted into the DAC REV C design... which explains why that board had issues powering up after assembly. DAC REV C Boards will require the same rework as the REV B.

This issue is to be resolved in the "DAC REV D" design.

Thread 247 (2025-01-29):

Update AMDC uInverter REV-C BOM

mohamed-dek1, 2025-01-29:
@elsevers

##
Should I create a PR that adds the necessary 5-40 screws to the uInverter parts log? These are used to attach the Heatsinks and the MOSFETs and we currently need them as a part of [this issue.](https://github.com/Severson-Group/Lab/issues/234)

elsevers, 2025-01-31:
The micro inverter uses [MOSFET gate drivers](https://www.digikey.com/en/products/detail/littelfuse-gsd/IXDN614CI/2424705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) as switches. These gate drivers are in a TO-220 package where the body is electrically connected to pin 3.

This means:
1. we should place an insulating thermal pad between the TO-220 package and the heat sink. [Here](https://www.digikey.com/en/products/detail/wakefield-vette/CD-02-05-220/7070008) is an example product that is appropriately sized for a TO-220 package
2. We should use a nylon bolt and nut to secure the TO-220 gate driver to the heat sink. We should use the recommended bolt/nut size for a TO-220. I think this is the 4-40.

So, please add to the BOM:
1. an insulating thermal pad
2. a 4-40 nylon screw and nut pair

elsevers, 2025-02-03:
@niloofarramroodi and @noguchi-takahiro, note that I have just updated the above comment to include a discussion thread and the possibility of using a shouldered washer.

elsevers, 2025-02-04:
See page 22 of our power stack's [manual](https://drive.google.com/open?id=1tFRP3jgKel58_gy9TGWC_Hh4EHQLk1PX&usp=drive_fs) for more guidance on this
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

Key items:
- use 4-40 screw and locking washer
- avoid nylon as it will melt under high temperatures

I see that you can search for insulating washers for heat sinks on [Mouser](https://hr.mouser.com/c/thermal-management/?type=Insulating%20Washer)

mohamed-dek1, 2025-02-05:
## Update

I've found the following which could be used.

- [MACHINE SCREW PAN PHILLIPS 4-40](https://www.digikey.com/en/products/detail/b-f-fastener-supply/PMS-440-0025-PH/49819)
- [HEX NUT 1/4" 4-40](https://www.digikey.com/en/products/detail/b-f-fastener-supply/HNZ-440/5738)
- [THERM PAD 17.78MMX12.7MM ORANGE](https://www.digikey.com/en/products/detail/wakefield-vette/CD-02-05-220/7070008)

I've tried looking for a set of insulating screws and a washer/nut combo but most of them were nylon. The set that I found is made of zinc. The thermal pad is the one that @elsevers sent as it is meant for the TO-220 package

mohamed-dek1, 2025-02-05:
@elsevers
The half bridges currently use a screw, hex nut, and thermal pad to secure the heatsink.

## Front
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

## Top
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

## Back
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

elsevers, 2025-02-06:
Alright, it sounding like we aren't really following the best practices all around.

Check out this kit on Mouser ([532-4880SG](https://www.mouser.com/ProductDetail/Aavid/4880SG?qs=MnLw5eI5rfiaN93%2F8XQqcQ%3D%3D) $3.75) for mounting heat sinks. This snippet from their datasheet really clearly illustrates what is going on:

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

Notice their use of `item 2`, which is an insulating shoulder washer / bushing which is made from Polyphenylene instead of nylon. Here is a screenshot from Digikey:

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

They also use a lock washer and hex nut.  Everything is for a `# 4-40` screw size.

SO, we either order 1 of these kits per heat sink or we start purchasing all of the components on that list individually.

Let's have you go ahead and order 10 of these kits [532-4880SG](https://www.mouser.com/ProductDetail/Aavid/4880SG?qs=MnLw5eI5rfiaN93%2F8XQqcQ%3D%3D) and we'll try them out on our uInverters. When you get them in and try them out, show me and we'll come up with a plan for what to put on the BOM.

elsevers, 2025-02-06:
I created an issue for purchasing these here: https://github.com/Severson-Group/Lab/issues/245

mohamed-dek1, 2025-02-14:
@elsevers, here's an update and a proposed plan for the mounting kit.

## Update
The mounting kits have arrived.
See this issue:
- https://github.com/Severson-Group/Lab/issues/245)

I've installed them onto my uInverter as shown below.

## Front
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

## Top
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

## Back
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

## Plan
Setup a uInverter **with** the mounting kit installed (mine) and another one **without** it (@mhmokhtarabadi). Get both hooked up to an AMDC with the same test and observe how each one does.

symen013, 2025-02-19:
@mohamed-dek1, what is the status of this issue? Is there anything I can help with?

mohamed-dek1, 2025-02-19:
@symen013 thanks for the reminder, I was waiting on a response from @elsevers on moving forward with testing the new thermal kits. If the kits work out, I will make a PR configured to close this issue that adds the components to the uInverter REVC BOM.

Closed 2025-03-01.

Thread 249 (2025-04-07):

Update REV20231005F readme for AMDC to standardize on information we provide for ordering boards

elsevers, 2025-04-07:
# Abstract
Update [REV20231005F/README.md](https://github.com/Severson-Group/AMDC-Hardware/tree/develop/REV20231005F) to standardize on information we provide for ordering boards

# Context
We are currently updating the AMDS information, see here:
- https://github.com/Severson-Group/AMDS/pull/55
- https://github.com/Severson-Group/AMDS/issues/54

We want to standardize on the information we provide for ordering assembled boards to make ordering easier in the future.

# Approach
Complete https://github.com/Severson-Group/AMDS/pull/55 first, and then close this issue via a PR that updates the [REV20231005F/README.md](https://github.com/Severson-Group/AMDC-Hardware/tree/develop/REV20231005F) file.

mohamed-dek1, 2025-04-17:
The following PR has been made to close this issue:

- #255

Closed 2025-04-18.

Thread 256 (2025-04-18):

Update REV20231005F release BOM to have a more professional description of parts

elsevers, 2025-04-18:
# Abstract

Update [AMDC REV20231005F release BOM](https://github.com/Severson-Group/AMDC-Hardware/blob/41687786357d77d512ec60de9c2c8b59ef2dacaf/REV20231005F/BOM_RevF.csv) to have a more professional description of parts

# Context

The [AMDS BOM](https://github.com/Severson-Group/AMDS/blob/develop/Mainboard/REV20200920D/mainboard-bom.csv) very nicely handles `Supplier Part Number`, `Manufacturer Part Number`, and `Description`

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

The [AMDC BOM](https://github.com/Severson-Group/AMDC-Hardware/blob/41687786357d77d512ec60de9c2c8b59ef2dacaf/REV20231005F/BOM_RevF.csv) does not fully handle this information:

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

We're missing a distinction between `Supplier Part Number` vs `Manufacturer Part Number`. The `Description` field seems to be partially split between a `Comment` and `Value` field.

# Approach
Close this issue via a PR that updates the [AMDC BOM](https://github.com/Severson-Group/AMDC-Hardware/blob/41687786357d77d512ec60de9c2c8b59ef2dacaf/REV20231005F/BOM_RevF.csv) to handle `Supplier Part Number`, `Manufacturer Part Number`, and `Description` in the same manner as the [AMDS BOM](https://github.com/Severson-Group/AMDS/blob/develop/Mainboard/REV20200920D/mainboard-bom.csv).

I do like that the [AMDC BOM](https://github.com/Severson-Group/AMDC-Hardware/blob/41687786357d77d512ec60de9c2c8b59ef2dacaf/REV20231005F/BOM_RevF.csv) has `Value` and `Footprint` fields. Let's maintain that.

This is probably best done by opening up Altium, fixing issues with in it, and regenerating.

mohamed-dek1, 2025-04-29:
This issue will be closed as it's task was completed here:

- #262

Closed 2025-04-29.

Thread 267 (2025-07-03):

Post to the discussion board to document how the eLev lab tests new AMDC boards

mohamed-dek1, 2025-07-03:
# Abstract
_To do: add one sentence description of what needs to happen_

# Context
We've recently been testing new AMDC boards and need to document how we are testing them for future reference.

- https://github.com/Severson-Group/Lab/issues/311

# Approach
- Write up a post to the discussion board that illustrates how the eLev lab tests a new AMDC board.

mohamed-dek1, 2025-07-16:
# DRAFT

TITLE: **AMDC REV F eLev Lab Testing Procedure**

##

> The following procedure documents how the eLev Lab tests new AMDC REV F boards.

# eLev Lab Testing Procedure For: AMDC REV F

## Out-the-box

1. Inspect the board for any obvious soldering issues or bridges.
    - If issues arise, try to fix them using flux and desoldering tools.
2.  Using a multimeter, inspect the board for possible shorts.
    - If issues arise, look for any `DNP` resistors that may have been populated mistakenly.
    - Inspect ICs near the short for any hardware issues.
3. Ensure all ports, DC-DC converters, and the Avnet PicoZed are populated.
4. Screw in all 13 standoffs using the ones listed in the BOM.
5. Label each board with a serial number based on the board logs.

## Bring-Up

6. Follow the instructions for the [REV F Bring-Up](https://docs.amdc.dev/hardware/revisions/rev-f/rev-f-bring-up.html).
7. Follow the instructions for [Building and Running Firmware](https://docs.amdc.dev/firmware/xilinx-tools/building-and-running-firmware.html).
8. After booting up the board, ensure that the LEDs begin blinking.
9. At this point, you should have an AMDC that can be flashed properly.

## Port Testing

### GPIO

10. Connect a working [uInverter](https://docs.amdc.dev/accessories/uinverter/index.html) and use a BNC to measure the current waveforms on an oscilloscope.

### POWER STACK | ANALOG

11. Connect a working [TestBoard](https://docs.amdc.dev/accessories/test-board/index.html).
12. Probe all PWM outputs using a logic analyzer like the Saleae, and ensure the correct signals at different switching frequencies and duty ratios.
13. Follow the [automated testing](https://github.com/Severson-Group/AMDC-Firmware/tree/develop/sdk/app_cpu1/common/usr/pcbtest) procedure to test the ADC and voltage rails.

### ENCODER

14. Connect the DB-9 from the encoder near bench 3 to the top encoder port on the AMDC.
> There is currently no firmware support for the bottom encoder port.
15. You will need to add firmware to read the encoder data in either an existing app ([blink](https://docs.amdc.dev/getting-started/tutorials/blink/index.html), [controller](https://docs.amdc.dev/getting-started/tutorials/vsi/index.html), etc) or create a [custom user app](https://docs.amdc.dev/firmware/xilinx-tools/create-user-app.html).
16. Rotate the encoder one revolution and poll the sensor.
17. Rotate again and ensure a new reading is polled.

### ETHERNET

18. Follow the [Host Interface](https://docs.amdc.dev/getting-started/user-guide/host-interface/index.html) instructions to setup the network adapter for the AMDC.
19. Read the [Python Wrapper](https://docs.amdc.dev/getting-started/user-guide/host-interface/python-wrapper.html) documentation to understand how to setup up a [Programmatic Interface With Python](https://docs.amdc.dev/getting-started/user-guide/host-interface/index.html#programmatic-interface-with-python).

## Optional

20. Switch the POWERSTACK `status` lines from `output` to `input` in hardware (jumpers) and firmware `sts_mux.h` and validate status of pins.
21. Remove the jumper for the `ESTOP` and see if the PWM output is disabled

## Resources

- [AMDC REV F Release Folder](https://github.com/Severson-Group/AMDC-Hardware/tree/develop/REV20231005F)
- [AMDC REV F docs](https://docs.amdc.dev/hardware/revisions/rev-f/index.html)

mohamed-dek1, 2025-07-16:
@knvprasad-dr, can you review this draft discussion post.

knvprasad-dr, 2025-07-17:
Per 7/17: @mohamed-dek1, this looks good to me. However, I have one suggestion to add some pictures to see what is expected at each important step.

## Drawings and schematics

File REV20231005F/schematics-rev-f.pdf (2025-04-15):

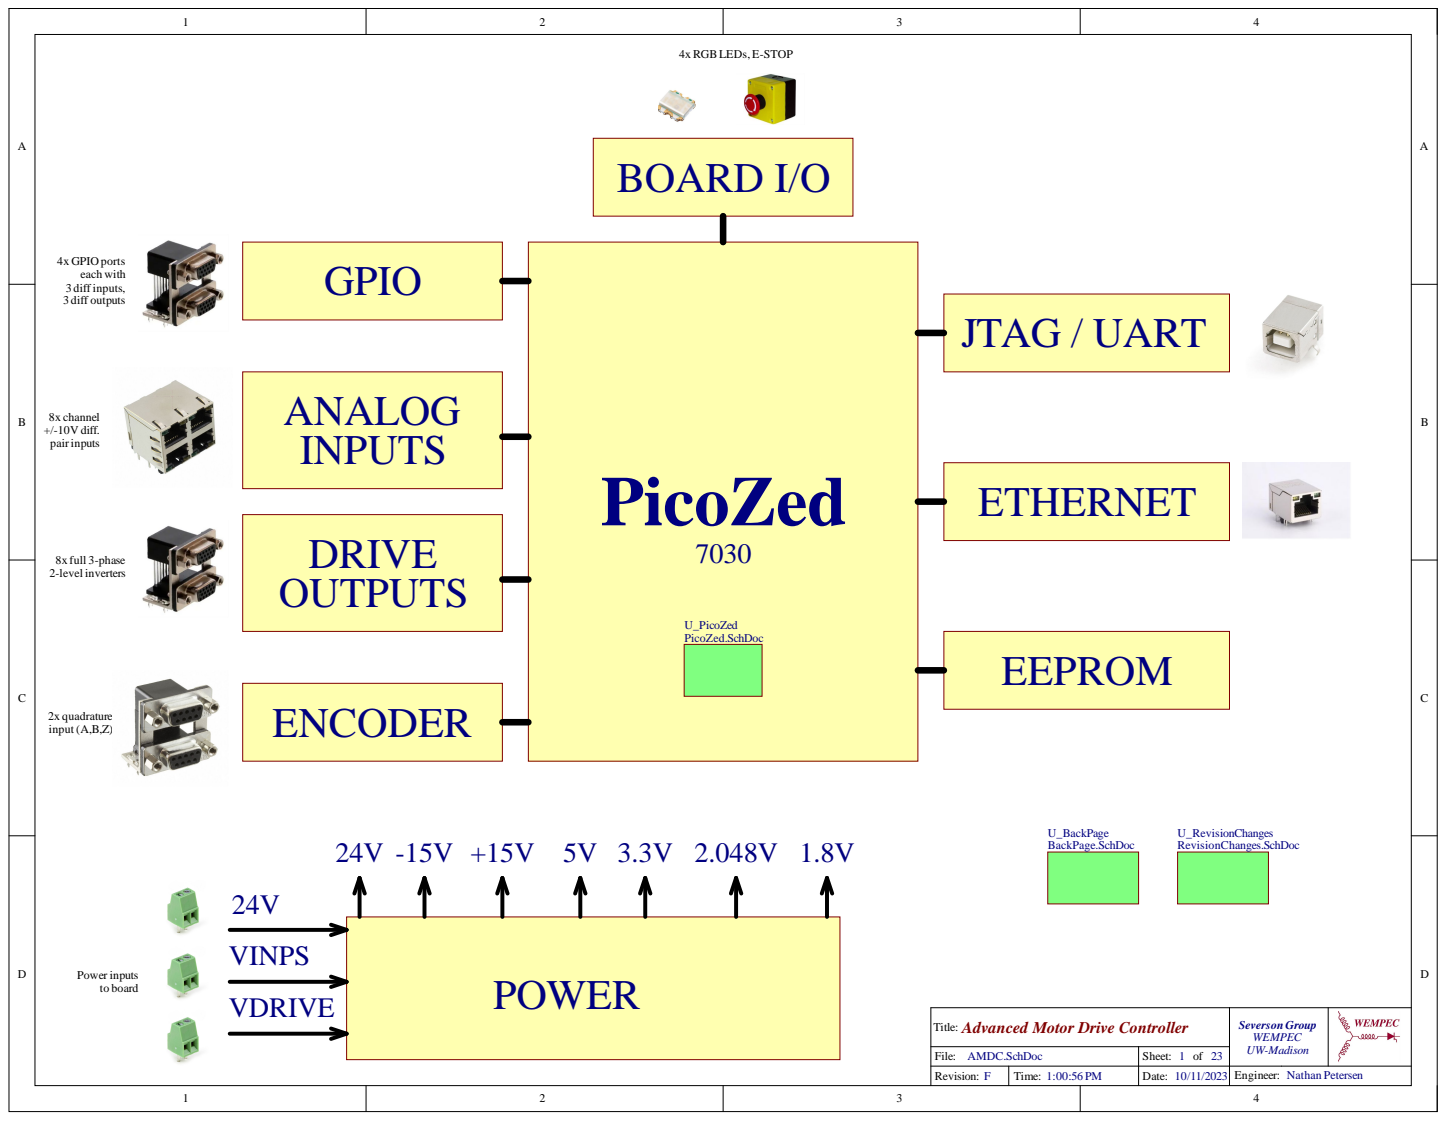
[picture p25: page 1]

Advanced Motor Drive Controller
Title:

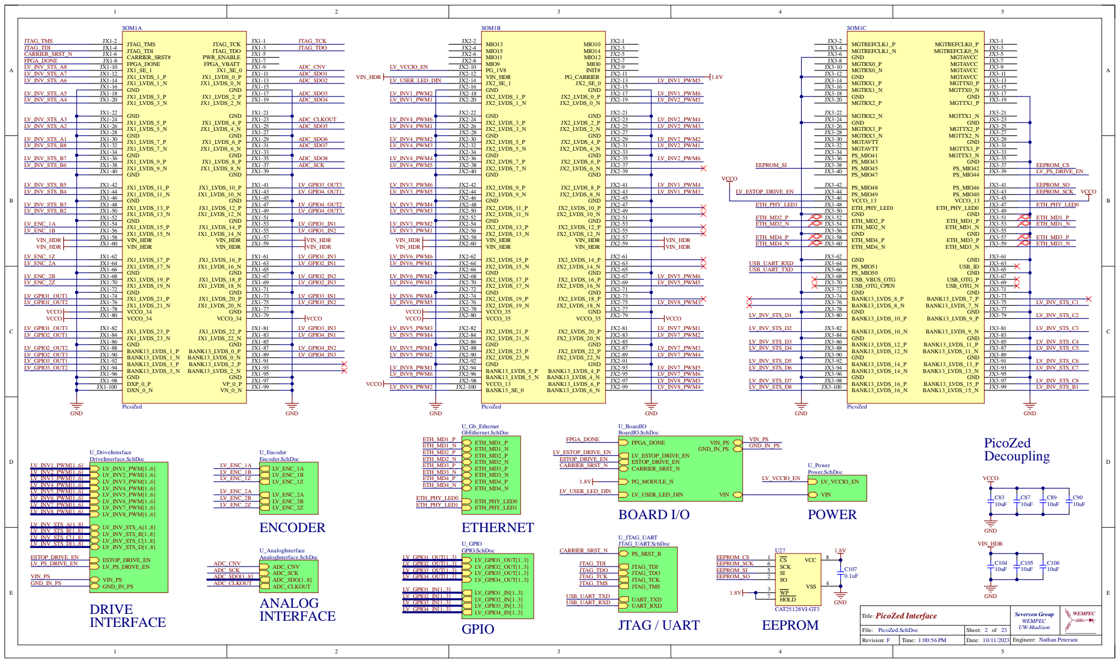
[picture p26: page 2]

GND JX3-56
ETH_MD4_P JX3-58

BANK13_LVDS_8_N JX3-76 | LV_INV_STS_C1
GND JX3-78 | LV_INV_STS_C2

File: PicoZed.SchDoc | Sheet: 2 of

Revision: F | Time: 1:00:56 PM | Date: 10/11/2023 | Engineer: Nathan Petersen

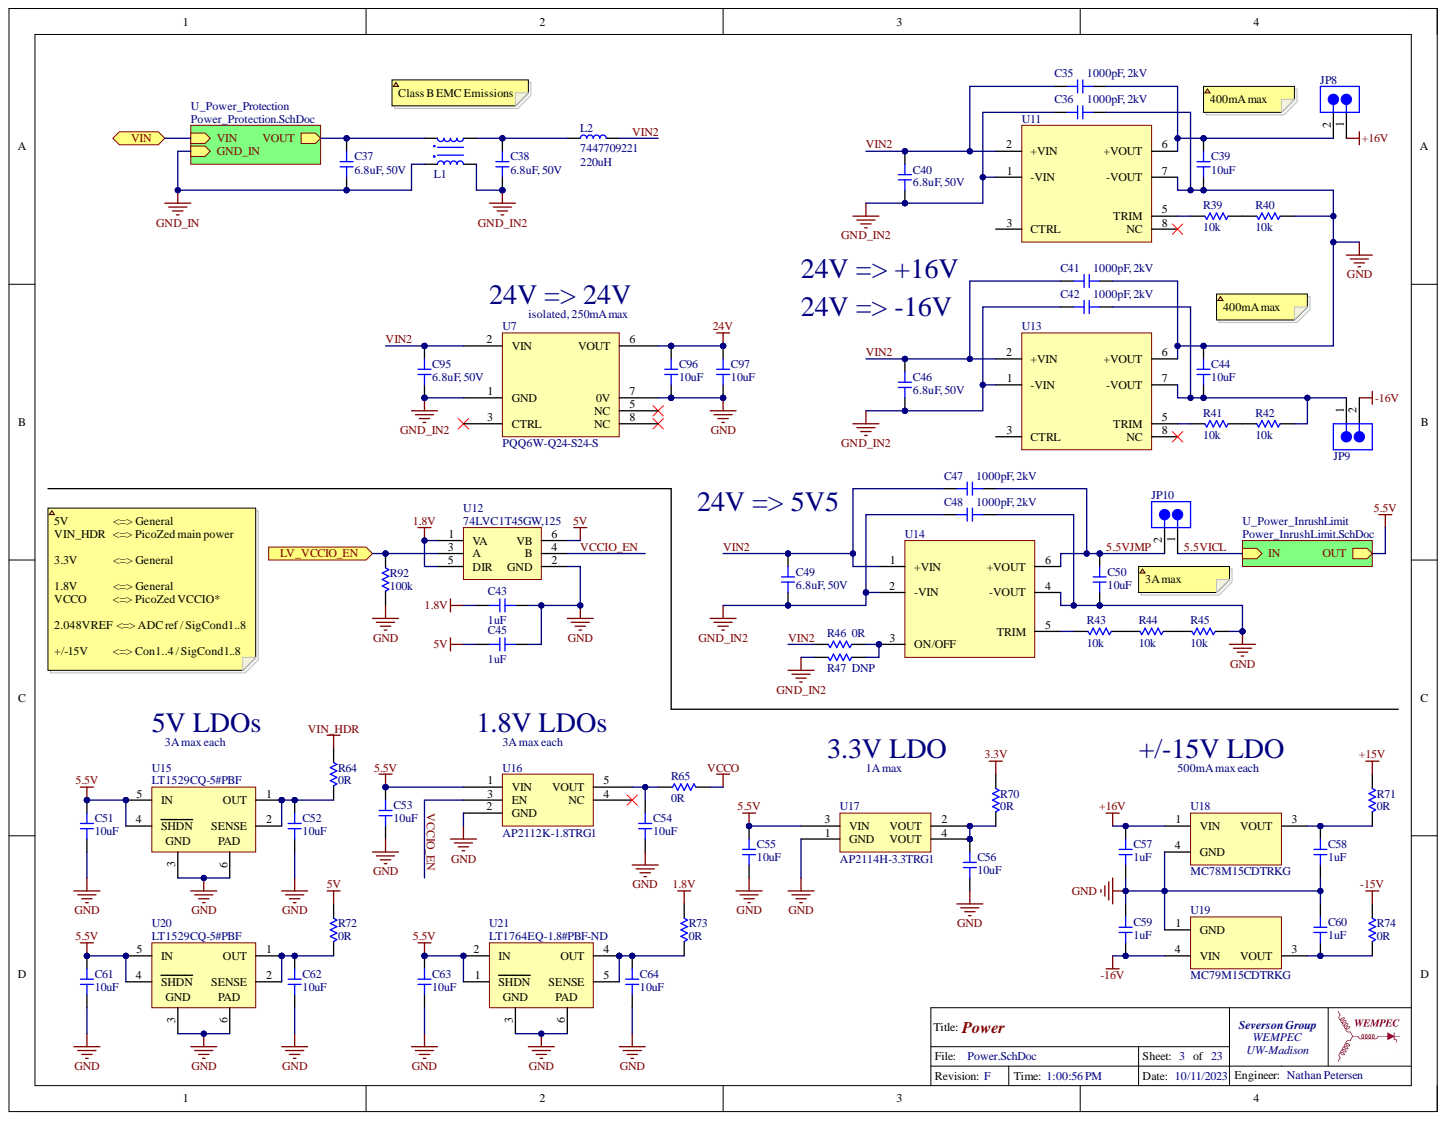
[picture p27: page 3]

+VOUT -VOUT | 6

-VIN 1 | 7

C46 | | -VIN 1
6.8uF, 50V

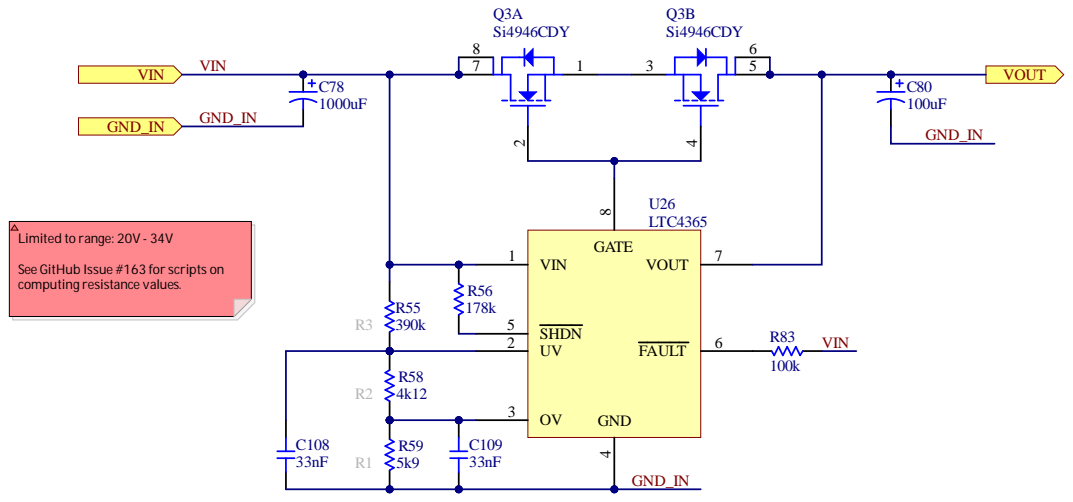
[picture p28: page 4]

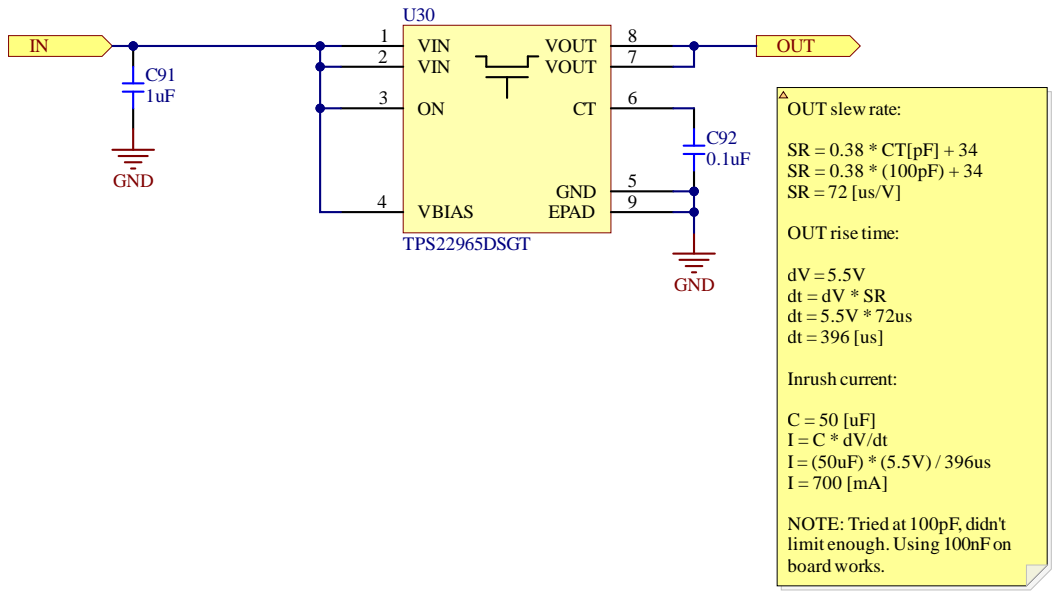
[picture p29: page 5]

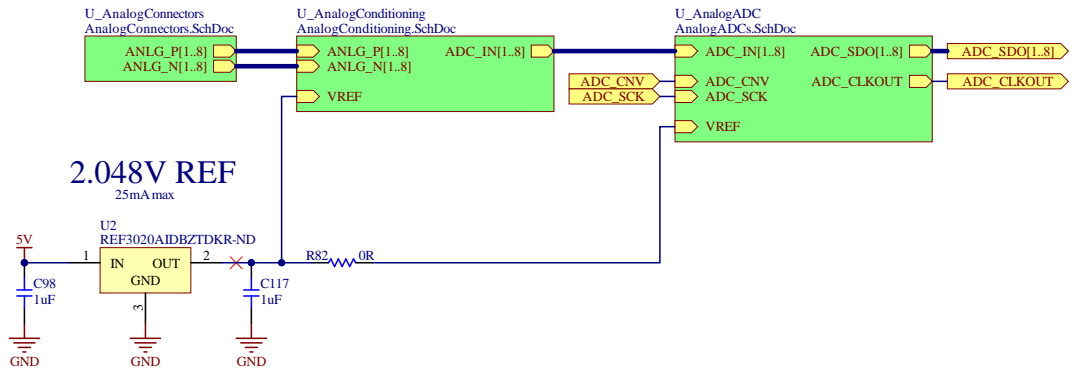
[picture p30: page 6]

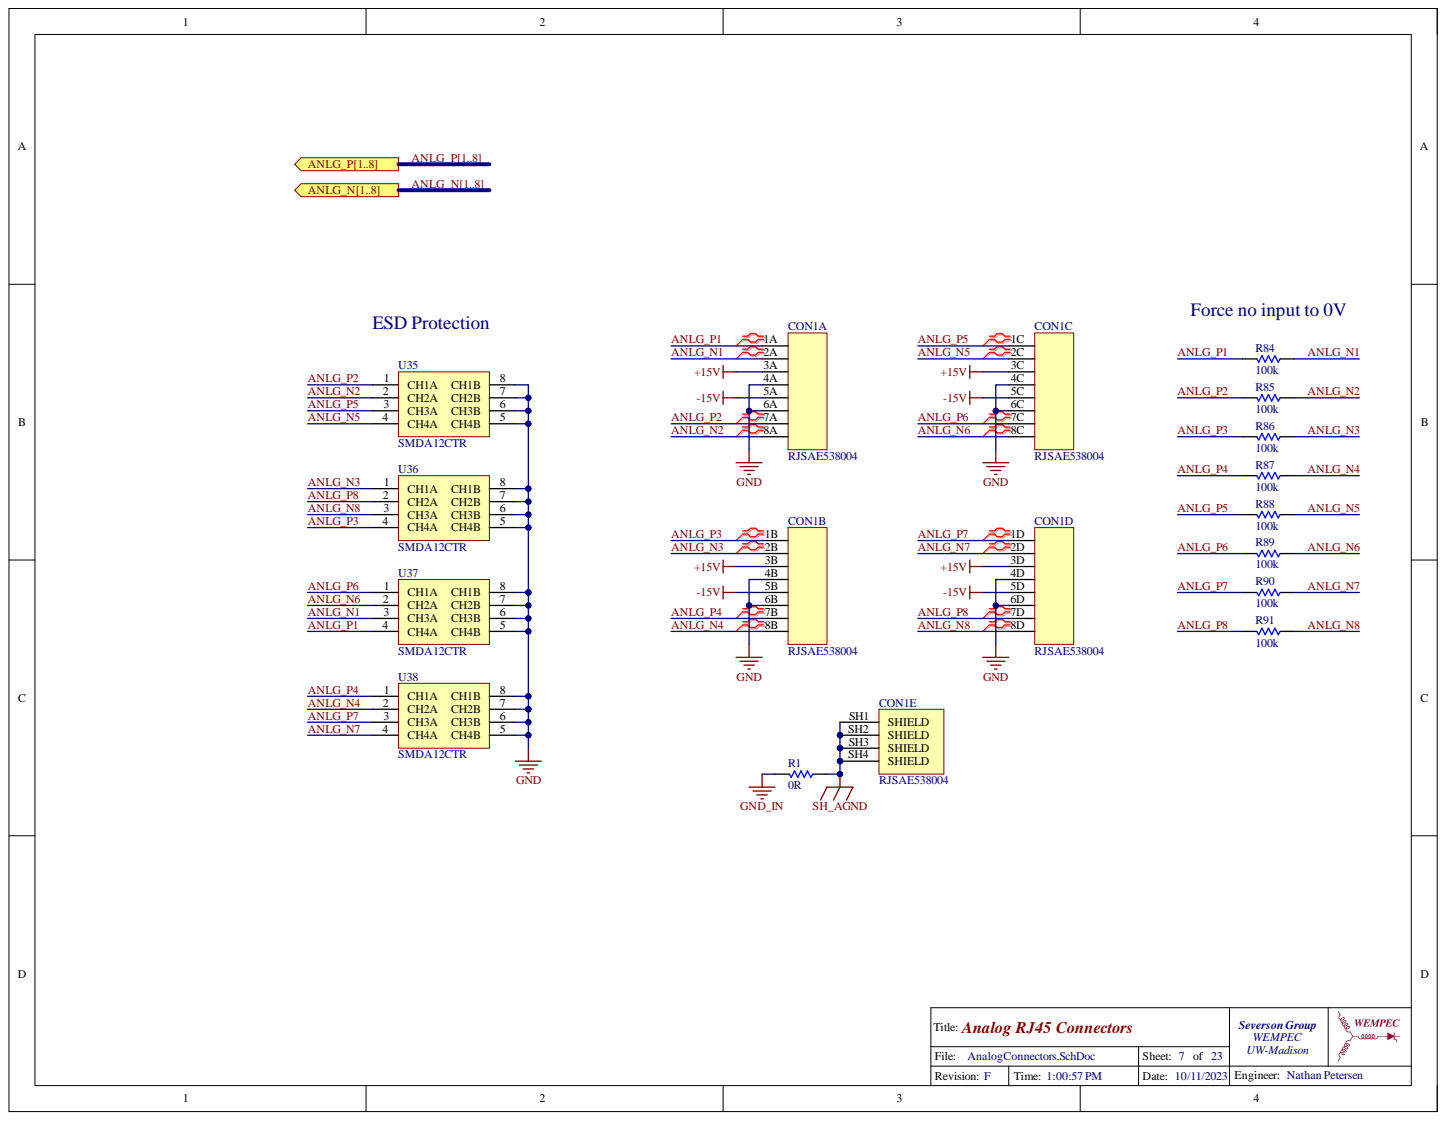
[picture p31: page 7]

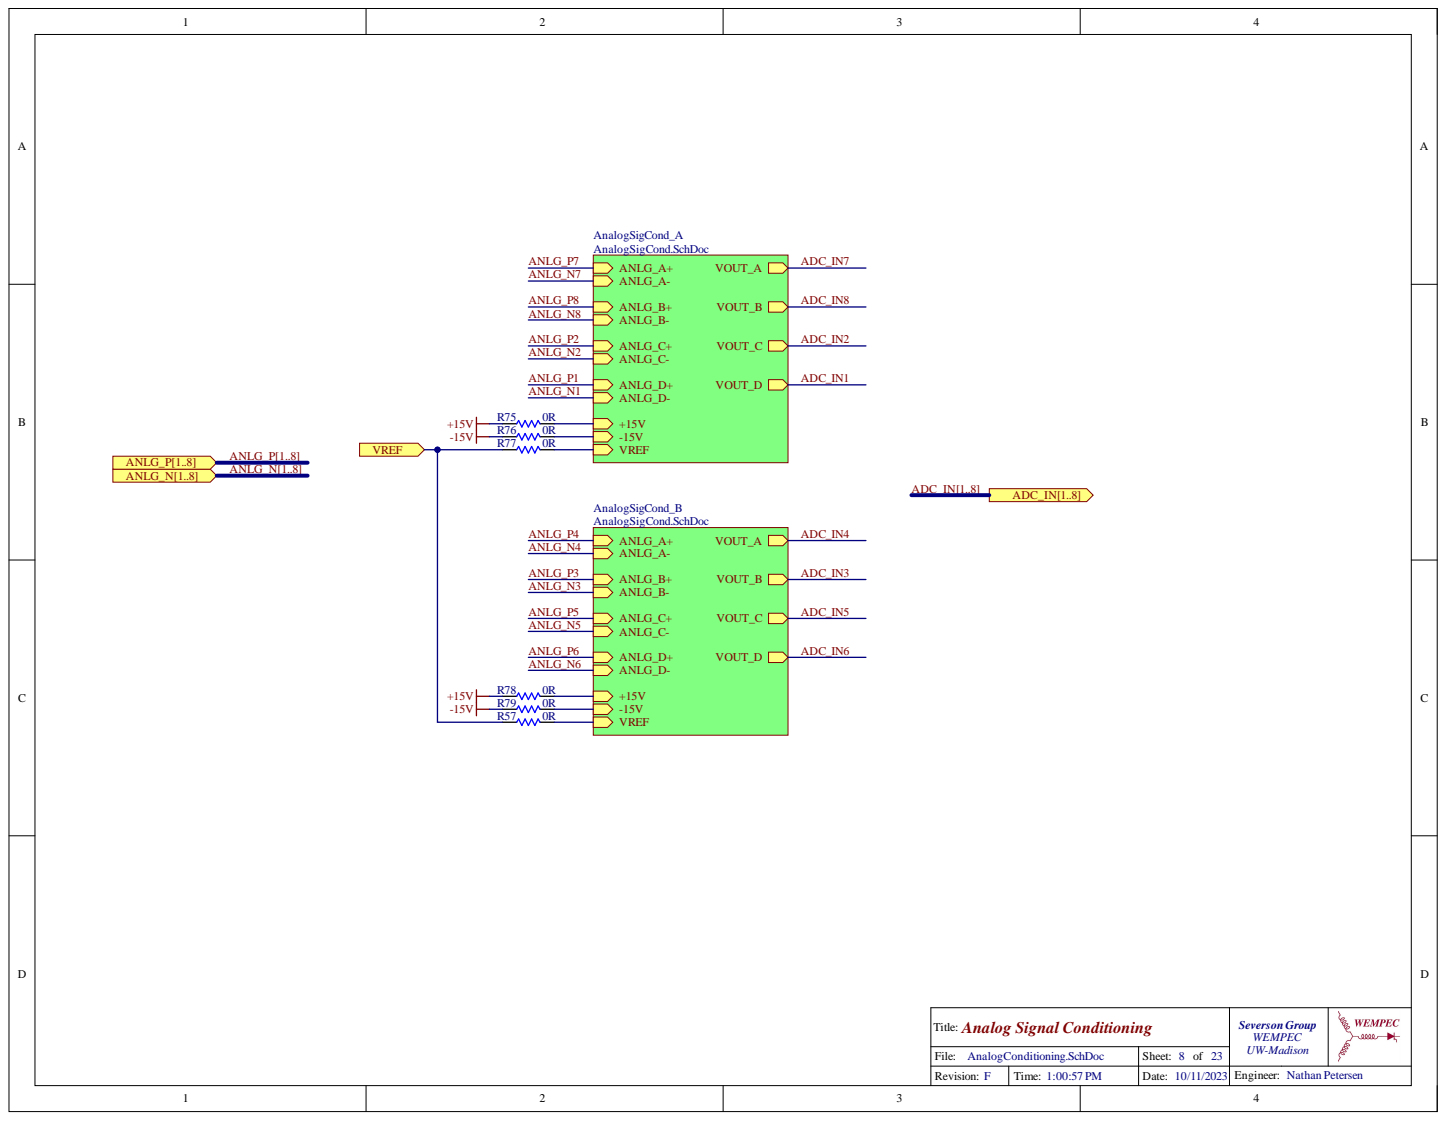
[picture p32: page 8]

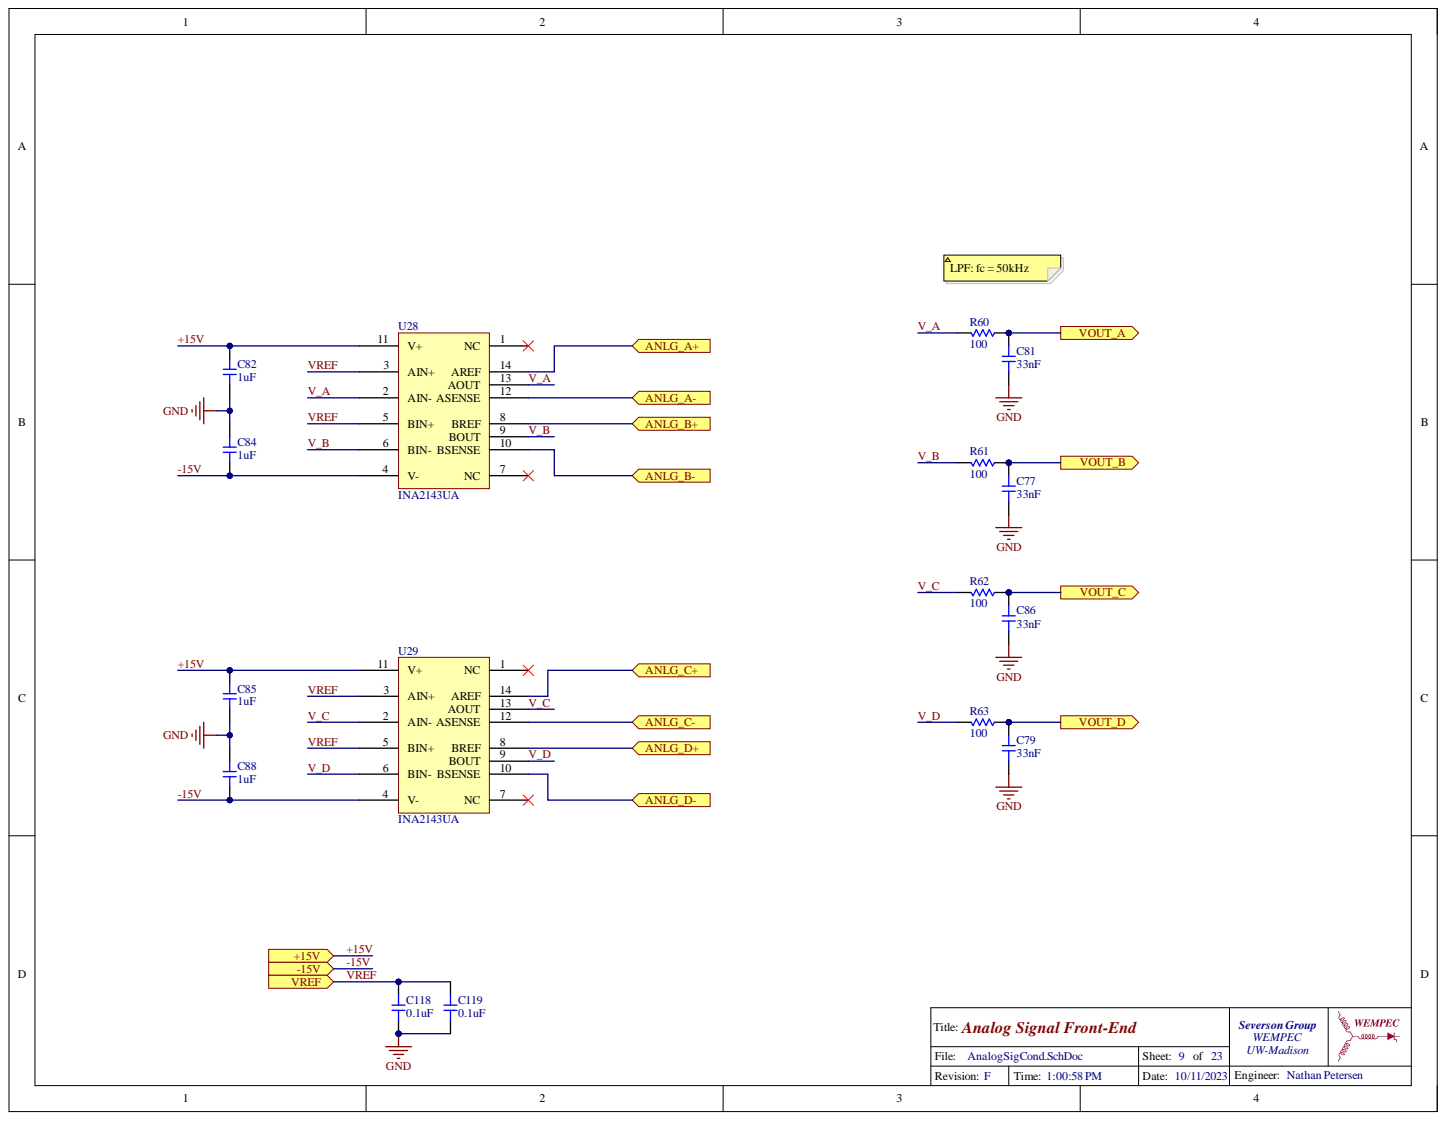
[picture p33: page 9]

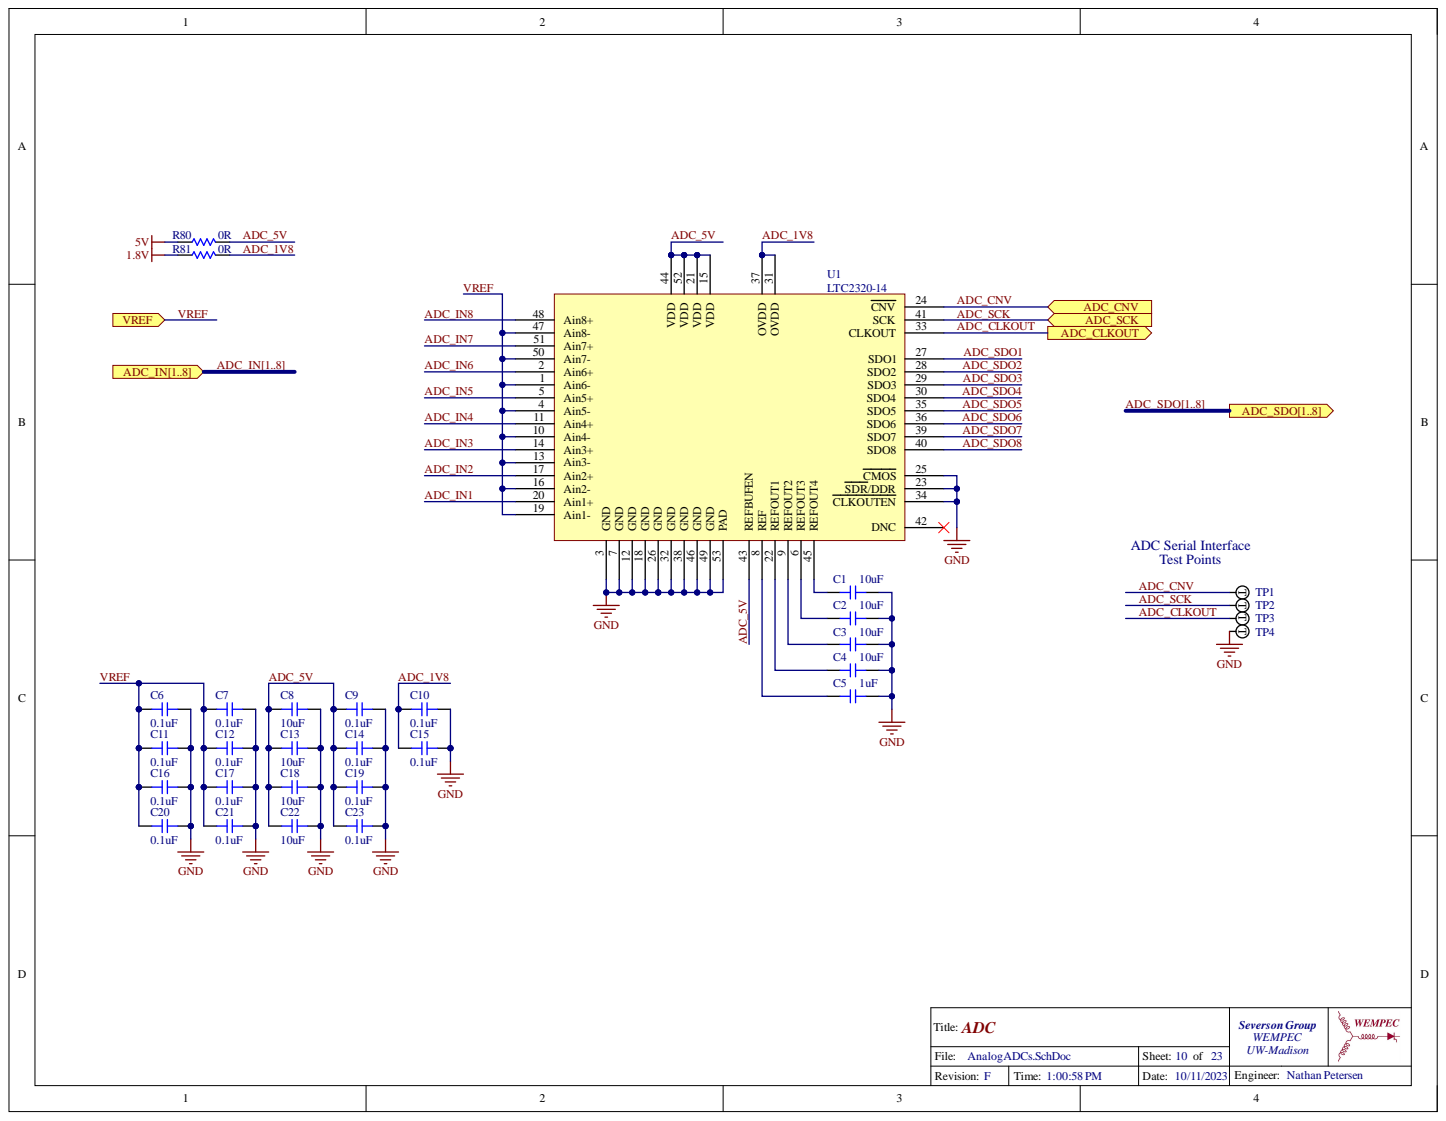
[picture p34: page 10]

ADC Serial Interface Test Points

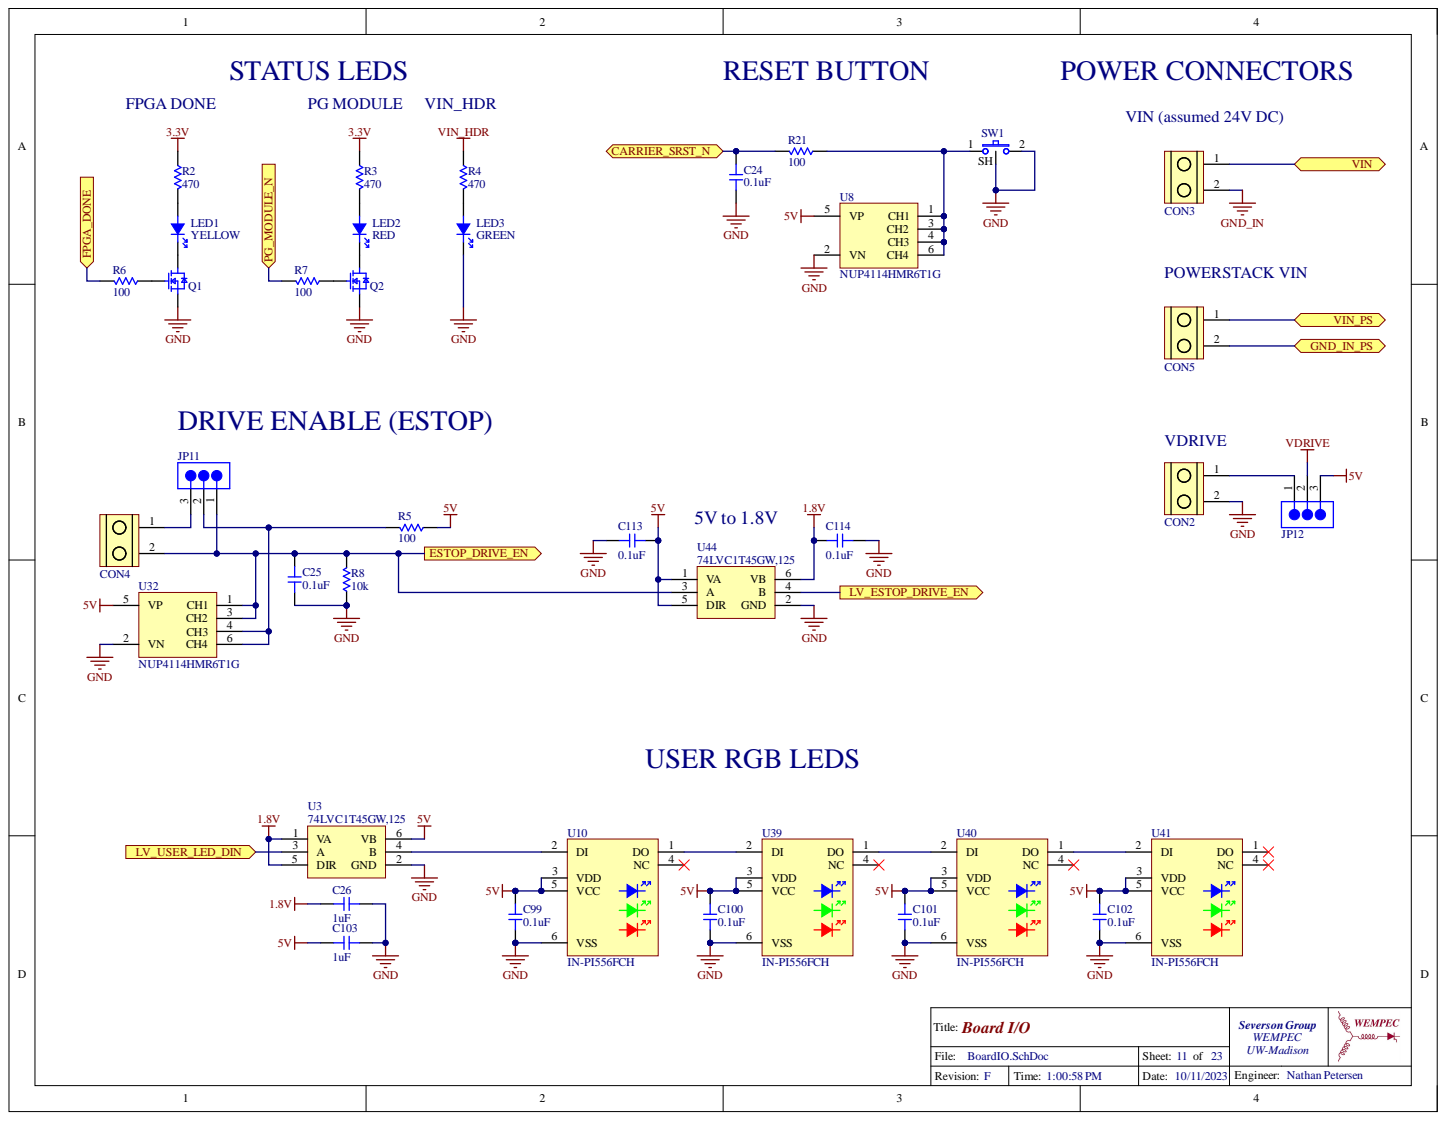
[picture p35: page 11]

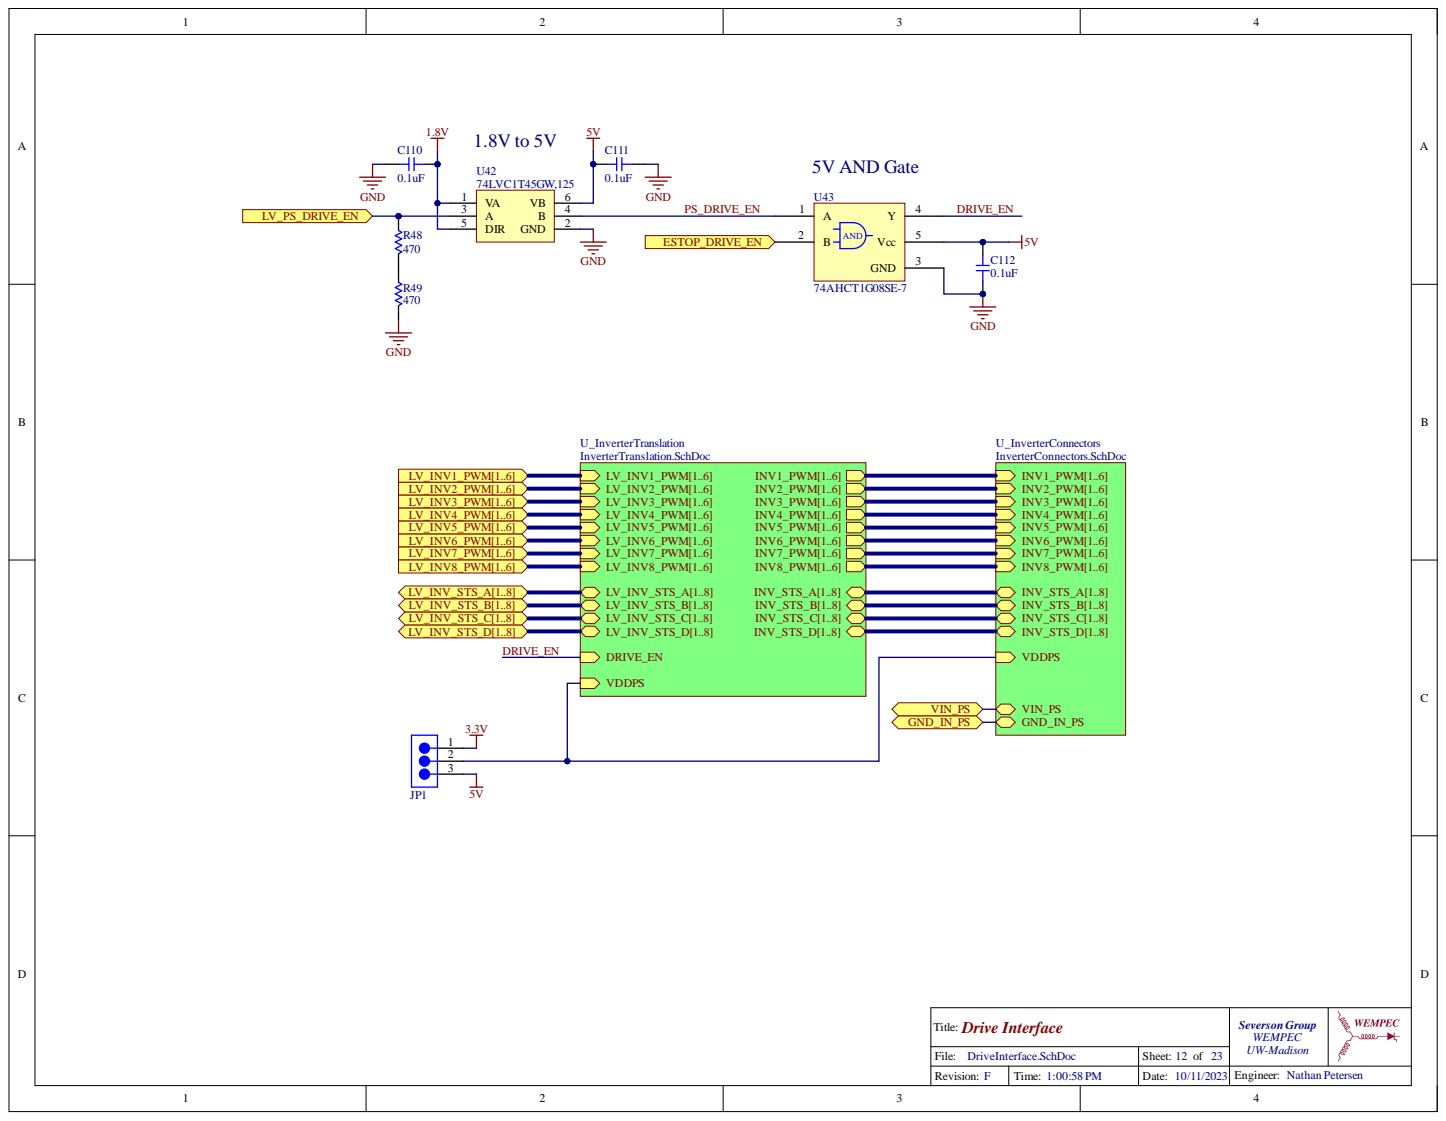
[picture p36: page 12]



2 | | 1 5 | 1 u C 7 | F 3
3 | | 1 4 1 3 1 2 1 1 8 D

2 0 | | | | G N
1 9 | | T C 4 4 6 8 E N U 2 5
1 8
1 7

2 | 1 5 | 1 u C 7 | F 6
3 | 1 1 8

1 0 | | 7


GND 12
GND 13




1 0 | 1 4

1 2
1 3


Title : | S e v erso n Gro up WEMPE C UW-Ma dis o n

File : GPIO. S c hDo c | S h e e t : 1 9 o f 2 3
Re visio n : | Tim e : 1:0 1:0 0 PM | Date : 1 0/1 1 /2 0 2 3 | En gin e e r : Nath a n P eterse n



V D D VREF_ J TA G | T M S T D I T D O T C K

2 USB _D _N
3 USB_ D _P | 1 7


Silkscreenmarked with default locations


- New PCB form factor (6" x 6.75", 6 layers)
- Add power stack supply rail distribution
- Add isoSPI ports
- Add extra encoder port
- Add 0R resistors to subsection power for debugging
- Add 100k resistors across analog inputs
- Add serially addressable RGB LEDs
- Add EEPROM
- Add fiducials to layout
- Remove user button / switch
- Remove discrete RGB LED
- Remove ADC2, now just one ADC
- Remove unity gain op-amp driving ADC inputs
- Reduce bulk input
- Reduce 24V power filter component current ratings
- Reduce 3V3 LDO current rating
- Change level-shifter IC for UART signals
- Change JTAG to NC module
- Change JTAG pin headers to pads
- Change values for inrush limiting circuitry
- Change FPGA driven MOSFETs to lower Vth
- Change FPGA pin-out mapping
- Change power stack connector I/O
- Change encoder input signal chain
- Change Ethernet routing to correct diff. impedance
- Fix footprints

- Remove isoSPI
- Add shared UART and JTAG interface
- Add more GPIO ports
- Add mechanical parts to BOM
- Add website to PCB silkscreen
- Add reset signal pull-up and ESD protection
- Add local decoupling to VREF
- Add local decoupling to 2.048V
- Add E-STOP logic signal to FPGA
- Add PTC resettable fuses to PWM outputs
- Add VDRIVE signal to PS interface
- Add jumpers for default VDRIVE and ESTOP
- Add pull-down to VCCIO_EN
- Change power wiring in schematics
- Change shield termination to VIN-
- Change mounting holes to VIN- from GND
- Change DB15 P/N to include screw posts
- Change to USB type B recepticle
- Update top-level block diagram
- Fix 24V supply to GPIO port
- Fix power protection circuitry
- Fix board start-up PWM issues
- Fix P/N for RC filter caps
- Fix BOM components for DFM

- Add power input protection
- Add test points
- Add TVS to analog inputs
- Change power input DC/DC modules
- Fix BOM with correct part numbers

- Add inrush current limiting to 5V5 rail
- Add more silkscreen labels
- Change ADC reference from 2.5V to 2.048V
- Change trim resistors for +/-16V DC/DCs
- Swap UART Tx / Rx pins
- Separate power stack shields between connectors

- Add termination on GPIO differential inputs
- Update pull-down resistor value for boot-up PWM
output protection
- Update P/Ns and footprints for manufacturability

See www.github.com/Severson-Group/AMDC-Hardware/issues for more discussion on design changes

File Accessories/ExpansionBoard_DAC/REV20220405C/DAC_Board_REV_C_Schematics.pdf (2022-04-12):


CON1 can be
conneted to both the
power stack and
GPIO connectors.
JumpersJ1-J5 are
used to configure the
DAC between the
powerstack and GPIO
pinouts.

JumpersJ6-J8 are
used to disable U1
when the power stack
is not in use

3 INV_STS_B | VIC 5 | INV_STS_C_ISO



OP Amp Power Supply


Silkscreen marked with default locations

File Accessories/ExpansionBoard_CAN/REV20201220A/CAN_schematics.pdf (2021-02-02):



14 GND2 15 VISOIN 16 3 CANH 1


14 GND2 15 VISOIN 16 3 CANH 1


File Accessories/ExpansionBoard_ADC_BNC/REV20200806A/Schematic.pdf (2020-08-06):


ADC Breakout to BNC
Title:

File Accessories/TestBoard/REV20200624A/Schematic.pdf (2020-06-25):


Voltage Rail Test Points


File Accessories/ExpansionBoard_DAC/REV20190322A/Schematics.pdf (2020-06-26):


AMDC DAC Expansion Card
Title:

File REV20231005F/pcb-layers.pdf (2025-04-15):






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


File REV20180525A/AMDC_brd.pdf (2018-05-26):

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

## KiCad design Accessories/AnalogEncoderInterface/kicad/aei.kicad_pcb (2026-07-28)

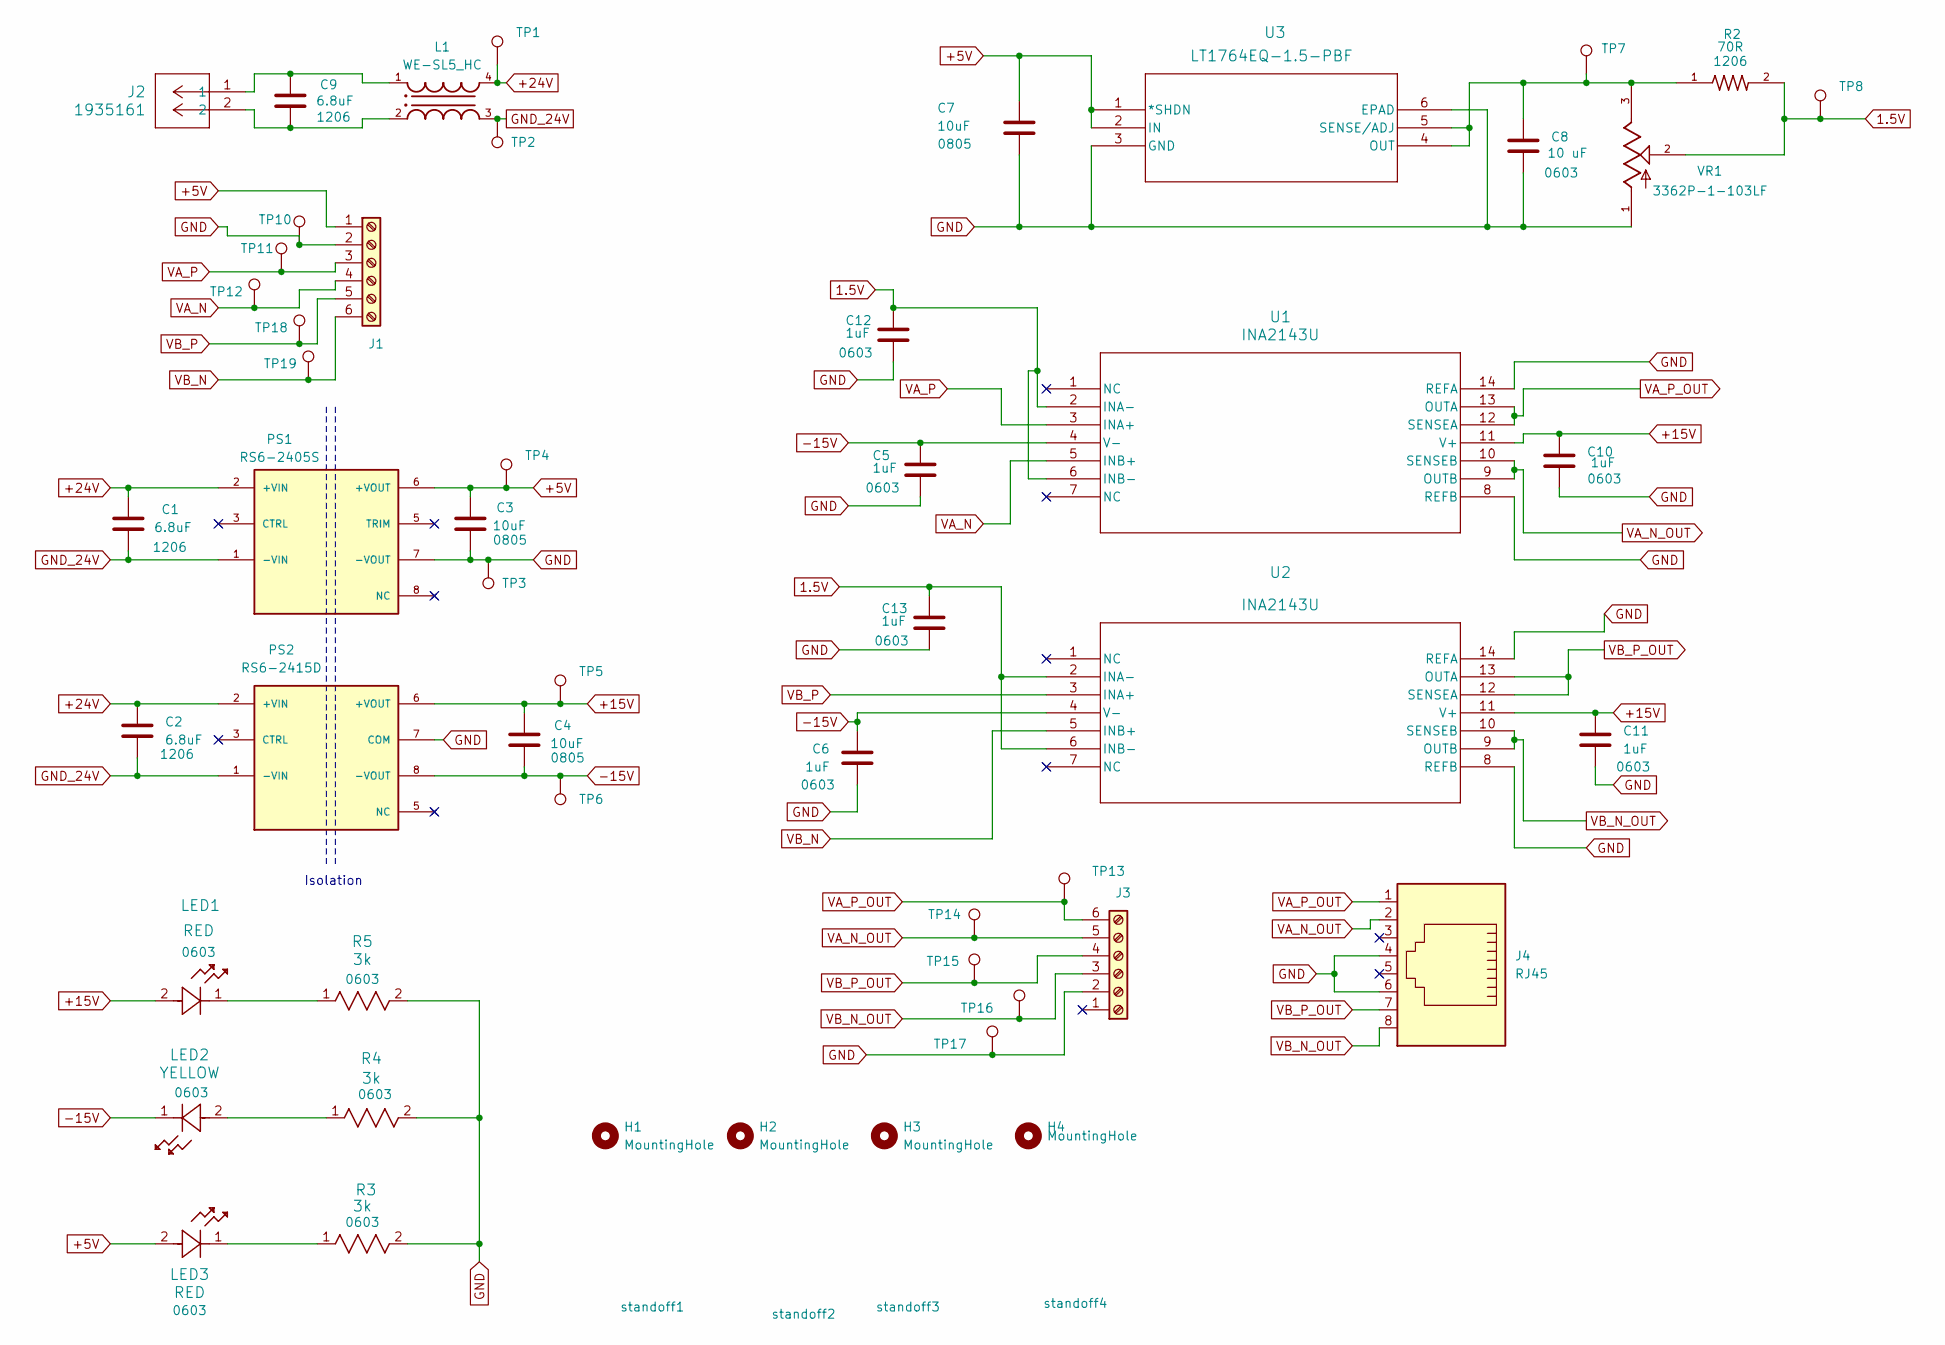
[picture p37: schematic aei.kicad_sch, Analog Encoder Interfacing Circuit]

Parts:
C1, C2, C9: 6.8uF; C_1206_3216Metric_Pad1.33x1.80mm_HandSolder
C3, C4, C7: 10uF; C_0805_2012Metric_Pad1.18x1.45mm_HandSolder
C5, C6, C10, C11, C12, C13: 1uF; C_0603_1608Metric_Pad1.08x0.95mm_HandSolder
C8: 10 uF; C_0603_1608Metric_Pad1.08x0.95mm_HandSolder
H1, H2, H3, H4: MountingHole; MountingHole_3.2mm_M3_DIN965_Pad_TopBottom
J1, J3: Screw_Terminal_01x06; TerminalBlock_Phoenix_MKDS-1,5-6_1x06_P5.00mm_Horizontal
J2: 1935161; TerminalBlock_Phoenix_MKDS-1,5-2_1x02_P5.00mm_Horizontal
J4: RJ45; RJ45_Amphenol_RJHSE5380
L1: WE-SL5_HC; DigiKey_Part_Number 732-2214-1-ND
LED1, LED3: RED; LED_0603_1608Metric_Pad1.05x0.95mm_HandSolder
LED2: YELLOW; LED_0603_1608Metric_Pad1.05x0.95mm_HandSolder
PS1: RS6-2405S; CONV_RS6-2405S; PARTREV 7
PS2: RS6-2415D; CONV_RS6-2415D; PARTREV 7
R2: 70R; R_1206_3216Metric_Pad1.30x1.75mm_HandSolder
R3, R4, R5: 3k; R_0603_1608Metric_Pad0.98x0.95mm_HandSolder
TP1, TP2, TP3, TP4, TP5, TP6, TP7, TP8, TP10, TP11, TP12, TP13, TP14, TP15, TP16, TP17, TP18, TP19: TestPoint; TestPoint_Keystone_5000-5004_Miniature
U1, U2: INA2143U; D14
U3: LT1764EQ-1.5-PBF; DDPAK-5_Q_LIT
VR1: 3362P-1-103LF; TRIM_3362P-1-103LF; PARTREV 08/26/10; DigiKey_Part_Number 3362P-103LF-ND
standoff1, standoff2, standoff3, standoff4: (no value)

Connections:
1.5V: C12.1, C13.1, R2.2, TP8.1, U1.2 (INA-), U1.6 (INB-), U2.2 (INA-), U2.6 (INB-), VR1.2
+5V: C3.1, C7.1, J1.1, LED3.2, PS1.6 (+VOUT), TP4.1, U3.1 (*SHDN), U3.2 (IN)
+15V: C4.1, C10.1, C11.1, LED1.2, PS2.6 (+VOUT), TP5.1, U1.11 (V+), U2.11 (V+)
+24V: C1.1, C2.1, L1.4, PS1.2 (+VIN), PS2.2 (+VIN), TP1.1
-15V: C4.2, C5.1, C6.1, LED2.1, PS2.8 (-VOUT), TP6.1, U1.4 (V-), U2.4 (V-)
GND: C3.2, C5.2, C6.2, C7.2, C8.2, C10.2, C11.2, C12.2, C13.2, J1.2, J3.2, J4.4, J4.6, PS1.7 (-VOUT), PS2.7 (COM), R3.2, R4.2, R5.2, TP3.1, TP10.1, TP17.1, U1.8 (REFB), U1.14 (REFA), U2.8 (REFB), U2.14 (REFA), U3.3 (GND), U3.6 (EPAD), VR1.1
GND_24V: C1.2, C2.2, L1.3, PS1.1 (-VIN), PS2.1 (-VIN), TP2.1
unnamed: C9.1, J2.1, L1.1
unnamed: C9.2, J2.2, L1.2
unnamed: LED1.1, R5.1
unnamed: LED2.2, R4.1
unnamed: LED3.1, R3.1
unnamed: C8.1, R2.1, TP7.1, U3.4 (OUT), U3.5 (SENSE/ADJ), VR1.3
VA_N: J1.4, TP12.1, U1.5 (INB+)
VA_N_OUT: J3.5, J4.2, TP14.1, U1.9 (OUTB), U1.10 (SENSEB)
VA_P: J1.3, TP11.1, U1.3 (INA+)
VA_P_OUT: J3.6, J4.1, TP13.1, U1.12 (SENSEA), U1.13 (OUTA)
VB_N: J1.6, TP19.1, U2.5 (INB+)
VB_N_OUT: J3.3, J4.8, TP16.1, U2.9 (OUTB), U2.10 (SENSEB)
VB_P: J1.5, TP18.1, U2.3 (INA+)
VB_P_OUT: J3.4, J4.7, TP15.1, U2.12 (SENSEA), U2.13 (OUTA)

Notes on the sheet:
Isolation

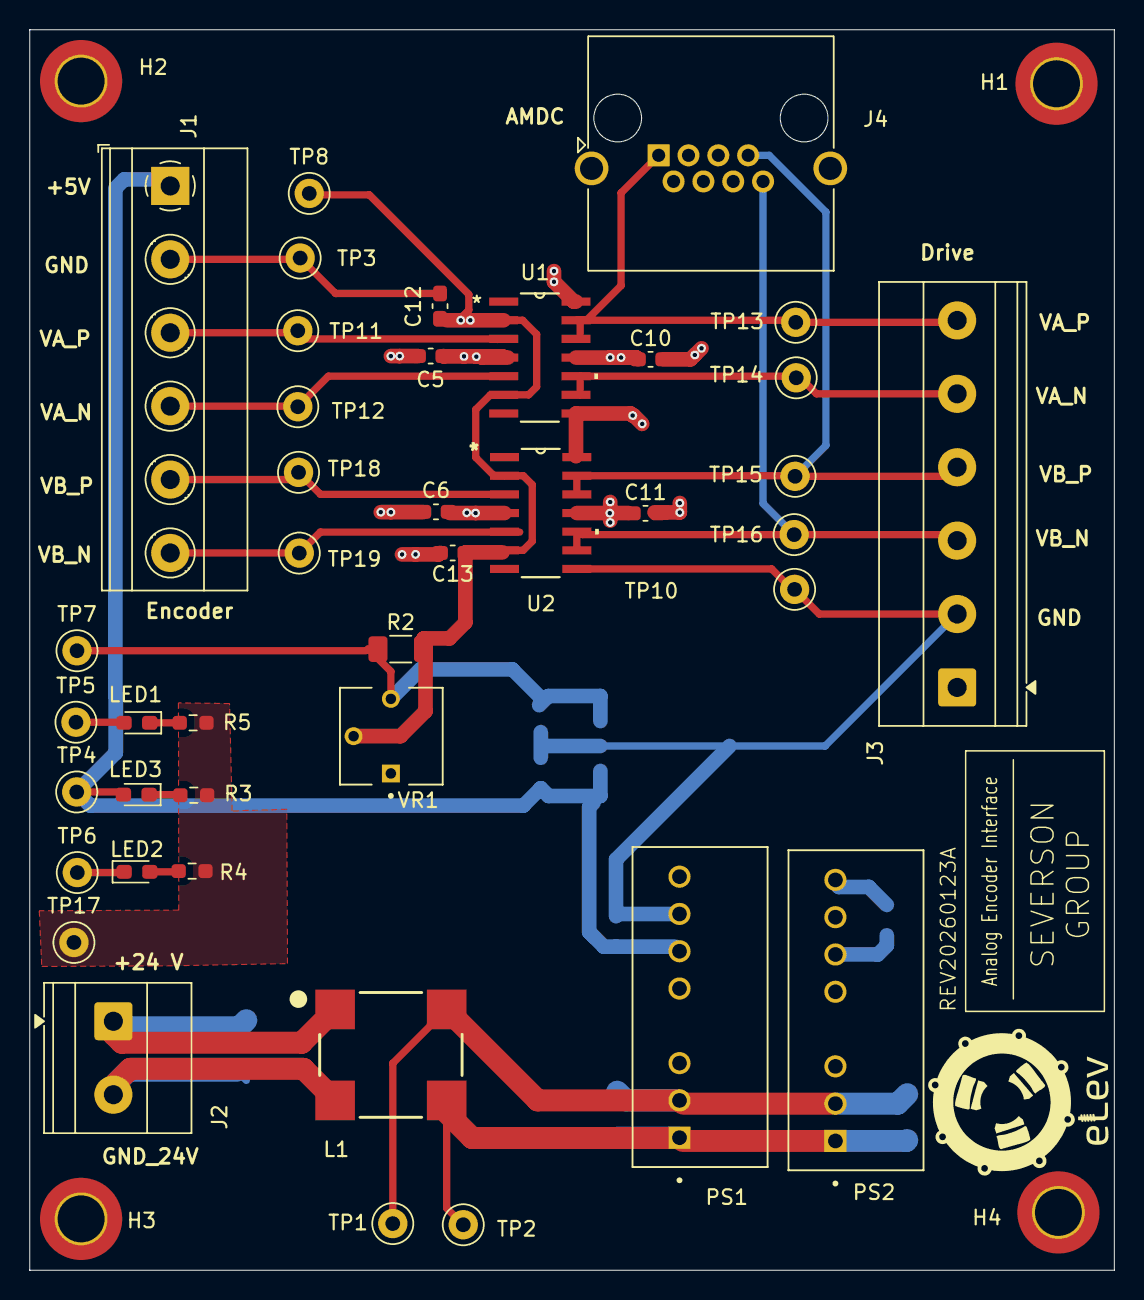
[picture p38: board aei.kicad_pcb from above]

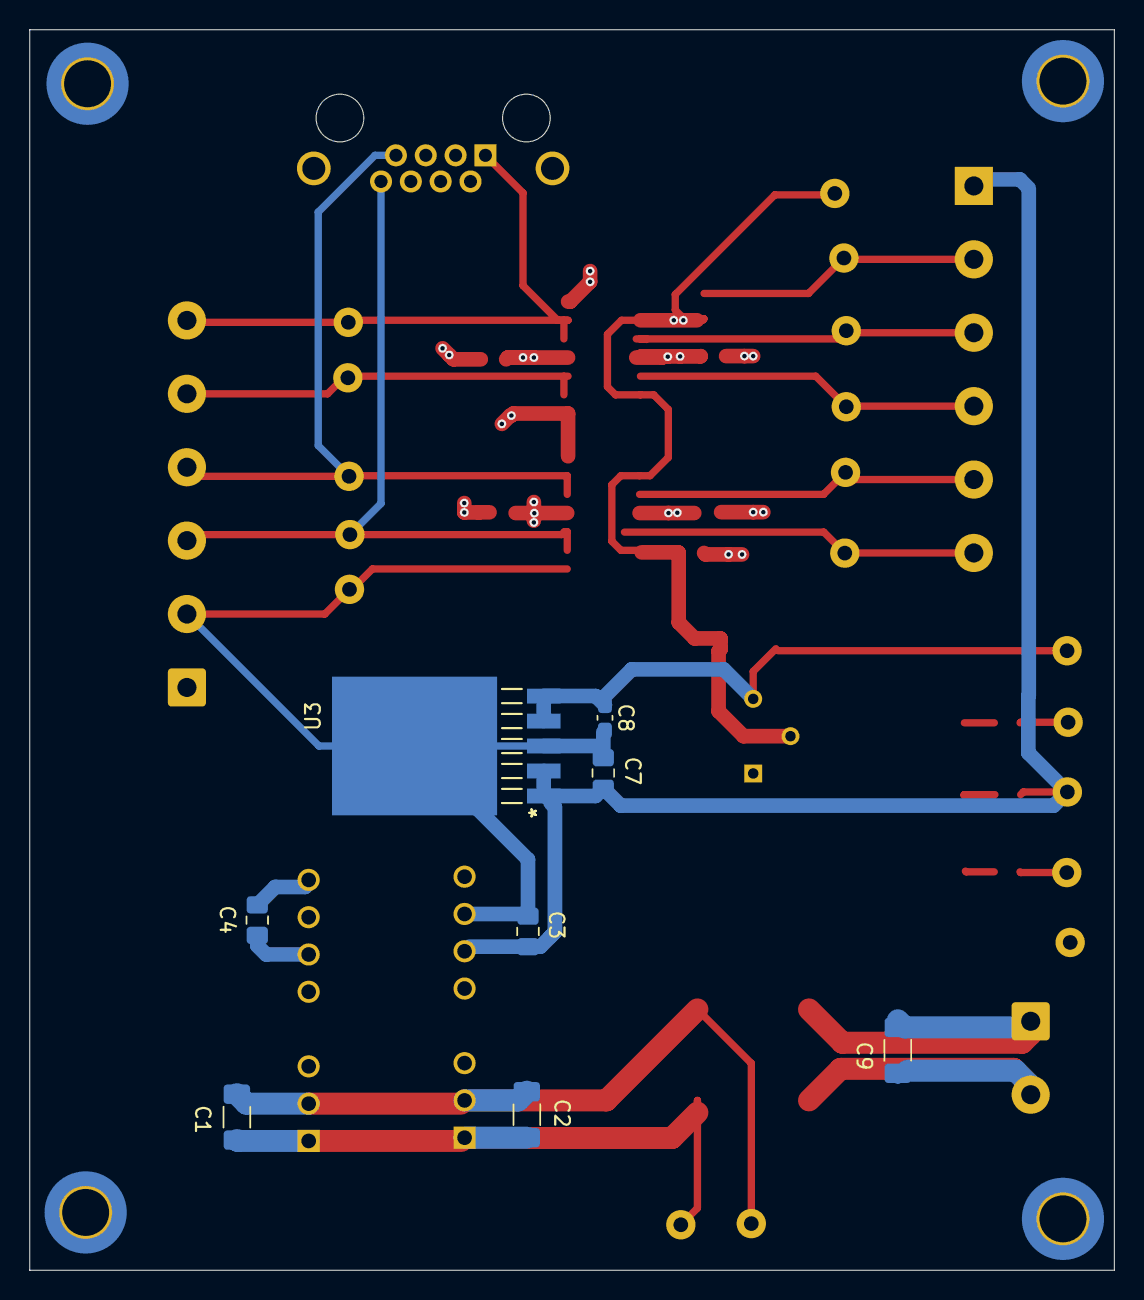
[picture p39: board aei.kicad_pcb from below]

Board: 4 copper layers, 73.9 x 84.5 mm, 53 parts (8 on the bottom side), 21 nets.

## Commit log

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2018-06-25 Design Validation Plan and Report (DVP&R)
    power supply validation done
    [AMDC DVP&R.xlsx]
2018-07-20 Add files via upload
    REV20180717B PRINTS, GERBERS, bom
    [AMDC_BOM.csv.xlsx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]
2018-07-31 Files for REV20180717B
    - This board has been ordered with these files.
    [AMDC.PrjPCB, AMDC.SchDoc, AMDC.SchLib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]
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2018-09-11 Revert "REV20180525A submitted files"
    This reverts commit 1bfddfe4aec15e84d899d8b9446b3ed9e708430a.
    [AMDC_BOM.xlsx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]
2018-09-23 Revert "Revert "REV20180525A submitted files""
    This reverts commit 19488338a9717da8e102e96dcb4ec9aaac1ef435.
    [AMDC_BOM.xlsx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]
2018-09-23 Fixed Altium schematic templates
    https://github.com/WEMPEC/AMDC-Hardware/issues/29
    [AMDC.SchDoc, AMDC.SchLib, AnalogADCs.SchDoc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]
2018-09-23 Fixed various issues
    I closed issues on GitHub for things fixed. This is dump of current project state.
    [0603cap.step, 0603led.step, 0603res.step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]
2018-09-28 More changes for REV C
    See GitHub Issues for what has changed.
    [AMDC.PrjPCB, AnalogADCs.SchDoc, InverterConnector.SchDoc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]
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2018-11-20 rearrange capacitors and fix net traces. Get rid of short circuit violations
    [AMDC.PrjPCB]
2018-11-20 Adjust designators of flipped capacitors. Route 1V8 node. Piano switch routing. 5V5 routing
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2019-09-02 Snapshot of work, mostly schematics and pulling into PCB
    [AMDC.PrjPCB, AMDC.SchDoc, AMDC.SchLib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]
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2020-01-14 More routing plus 100k res on analog inputs
    [AnalogConnectors.SchDoc]
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2020-01-20 All signals routed, now just clean-up etc to do
    [PicoZed.SchDoc, USB_UART.SchDoc]
2020-01-20 Clean up routing, plus add PicoZed power rail decoupling
    [PicoZed.SchDoc]
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2020-01-24 Finish ethernet routing with diff impedance and length matching
    [AMDC.PrjPCB]
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2020-01-29 Add EEPROM and Revision Changes page (update all page numbers)
    [AMDC.PrjPCB, AMDC.SchDoc, AnalogADCs.SchDoc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]
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2020-03-04 Fix UART and SPI peripheral numbers
2020-03-04 Add rework image for power protection
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2020-05-26 Fix example encoder problem
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2020-06-24 Updates from design review meeting, ready to order.
    [PCB.PcbDoc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]
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2020-07-06 Added standoffs and fixed schematic labels
    [BackPage.SchDoc, DAC.SchLib, DAC_Expansion_Board_Project.PrjPcb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]
2020-07-06 Replaced OP Amps with cheaper option
    [DAC.PcbLib, DAC.SchLib, DAC_Expansion_Board_Project.PrjPcb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]
2020-07-07 Added new power supply schematic symbols and footprints
    [CUI_PDME1-S5-D15-S.step, CUI_PDSE1-S5-S9-S.step, DAC.PcbLib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]
2020-07-08 Revert "Replaced OP Amps with cheaper option"
    This reverts commit 600ba64f3b8f51c2603ef18d2e4755111aaddf8d.
    [DAC_Expansion_Board_Project.PrjPcb, OutputConnectors.SchDoc]
2020-07-08 Updated schematic with quad pack op amps and cheaper DC-DC converters
    [DAC.PcbLib, DAC.SchDoc, DAC.SchLib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]
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2020-07-08 Added jumpers and pull down resistors to U1 and added signal diagram
    [DAC.SchDoc, DAC.SchLib, InputConnector.SchDoc]
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2020-07-09 R16 was old 1% tolerance resistor, updated to 0.1% tolerance resistor
    [DAC_bom_qty_1.xlsx, DAC_bom_qty_10.xlsx, OutputConnectors.SchDoc]
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2020-07-09 removed DNP resistor and mounting holes from BOM
    [BackPage.SchDoc, DAC.SchLib, DAC_bom_qty_1.xlsx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]
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2020-08-06 Add new ADC breakout board to BNC jacks
    [ADC_Breakout.PrjPcb, BOM.csv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]
2020-08-06 Fix test point part number
    [BOM.csv]
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2020-08-06 Fixed PCB-Electrical-Tests
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2020-10-26 I/O Converter REV A PCB Review (#145)
    * Added IO Converter Expansion Board
    * Restored AMDC PrjPCBStructure
    * Added README
    * Added 5V to 3.3V level translator
    * Updated PCB Properties
    * Added docs README and .csv BOM
    [IO_Converter.PcbLib, IO_Converter.SchDoc, IO_Converter.SchLib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]
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2021-02-02 CAN Board REVA Cherry-Picked PR (#153)
    * CAN board altium files
    * Add silkscreen
    * Update folder structure, documentation
    * Add jumper in series with resistor to AMDC connector
    * Upload gerbers
    * Update documentation
    * Rename README.MD to README.md
    * Update README.md
    * Fix date design was frozen
    [BackPage.SchDoc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]
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2021-02-26 Implemented about half of issues, committing as back-up
    [AMDC.PrjPCB, AMDC.SchLib, AnalogSigCond.SchDoc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]
2021-02-26 More issues done, largely JTAG and UART integration
    [AMDC.PrjPCB, AMDC.SchDoc, AMDC.SchLib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]
2021-02-26 More dev, mostly remove isoSPI and add more GPIO
    [AMDC.PrjPCB, AMDC.SchDoc, AnalogADCs.SchDoc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]
2021-02-27 Implemented remaining issues, mainly GPIO 24V isolated power, shield terminations
    [AMDC.SchDoc, AMDC.SchLib, AnalogADCs.SchDoc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]
2021-02-27 Create new PCB doc and import schematic changes, ready for layout
    [AMDC.SchDoc]
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2021-03-15 More routing + implemented a few GitHub issues; ~50 signals left to route
    [AMDC.PrjPCB, AnalogInterface.SchDoc, AnalogSigCond.SchDoc]
2021-03-15 More routing, fix bug in JTAG sch, 12 unrouted -- mostly power
    [JTAG_UART.SchDoc]
2021-03-17 Done with layout, design is ready for review!
    [BackPage.SchDoc, BoardIO.SchDoc]
2021-03-18 Corrections in Vdc, fsw, Iac ratings and update R_shunt resistor (from 0.25 to 0.15mohms) for these updates.
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2021-03-25 Updated BOM with shunt resistor for AC rms current rating. Added schematic snapshots.
    [Bom_uInverter.csv]
2021-03-25 Update PCB routing vias to be tented and constant size
    [AMDC.PrjPCB]
2021-03-25 Update shield term to be 0R by default, not DNP
    [AMDC.PrjPCB, AnalogConnectors.SchDoc, Encoder.SchDoc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]
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2021-03-25 Fix ESD protection on reset button
    [BoardIO.SchDoc]
2021-03-25 Update power schematic wiring, no functional changes, no PCB changes
    [AMDC.PrjPCB, AMDC.SchDoc, BackPage.SchDoc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]
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2021-04-13 Schematics update. Added component footprints. Components placed on PCB.
    [2021-03-01_23-58-07.PcbLib, 2021-03-01_23-58-07.SchLib, 2021-03-09_02-20-10.PcbLib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]
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2021-04-28 Added first set of docs - schematics and gerbers.
    [PCB1_01.GBL, PCB1_01.GBO, PCB1_01.GBP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]
2021-05-05 Added more test points, ground vias for decoupling capacitors. Removed unnecessary files and repo cleanup to follow standard folder structure. Minor silkscreen modifications. Included documentation.
    [Backpage.SchDoc, Bom_uInverter.csv, Half_bridge_load.SchDoc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]
2021-05-07 Cleanup of uinv-rev-a branch for clean comparison with uinv-rev-a-pcb branch.
    [Backpage.SchDoc, Bom_uInverter.csv, Half_bridge_load.SchDoc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]
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2021-05-07 meta-commit: to resolve conflicts in `uinv-rev-a` (cleaned up) and `uinv-rev-a-pcb`
    [Backpage.SchDoc, Half_bridge_load.SchDoc, PcbLib_uInverter.PcbLib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]
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2021-05-07 Minor modifications in README files and folders. Gerber zip removed.
    [Backpage.SchDoc, Half_bridge_load.SchDoc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]
2021-05-08 IO Converter REV B PCB Review (#178)
    * Added IO Converter REV B Files
    * Added R10 and R15 to BOM
    * Added bypass caps and test points
    * updated gerbers
    * Renamed IO expansion board
    * Updated docs and board diagram
    * information included on glitch filter operation
    * Added white background to svg
    * moved block diagram before filter section
    * Added External connectors header
    [IO_Converter.PcbLib, IO_Converter.SchDoc, IO_Converter.SchLib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]
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2022-04-11 uInverter revB (#208)
    * Initial revB schematic commit
    * Update revA BOM and add libraries
    * Correct revA BOM, revB changes as listed in PR
    * Change Altium file names, remove altium folder from revB
    * Add changelog.md
    * Update CHANGELOG.md
    * Update CHANGELOG.md
    * Update CHANGELOG.md
    * Update CHANGELOG.md
    * Reannotate PCB components and resolve DRC violations
    * Implement changes recommended in PCB review 1
    * Add revB folder
    * Update 3D image
    * Make changes as requested in PCB review 2
    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
    [Backpage.SchDoc, Half_bridge_load.SchDoc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]
2022-04-12 [DAC Board] Rev C Final Merge (#213)
    * Create new TVS diode in SchLib and update OutputConnectors schematic
    * Apply fix to TVS diodes on PCB Doc
    * Add "Patrick Nowakowski" to Engineer box
    * Remove IsoSPI Hardware from DAC Schematic
    * Add new REV C components to DAC SchLib
    * Add GPIO connections, conversion and isolation on DAC Input Connectors schematic
    * Make touchups to first review draft of DAC Rev C Schematic
    * Tweak DB-15 Connector labels on DAC InputConnector SchDoc
    * Update DAC REV C PcbDoc with new components
    * Create schematic symbol and footprint for SDA06H0SBR DIP switch
    * Fix DIP switch designator in DAC SchLib
    * Fix AM26C32 G connections and fix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
    [BOM_DAC_REV_C_Qty1.csv, BOM_DAC_REV_C_Qty10.csv, BackPage.SchDoc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]
2022-11-29 Add silkscreen designator column to BOM (#221)
    * Add silkscreen designator column to BOM
    * Change designator list order
    * Fix jumper designator
    * Add user note about issue 216 to README
    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
    [uInv_revB_BOM.csv]
2022-11-29 uInverter revision C (#220)
    * Fix component designators on PCB silkscreen
    * Create and incorporate fixes in revC
    * Add rev C fab files and picture
    [Half_bridge_load.SchDoc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]
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2023-03-20 [Kaman IO Converter Board] Rev C Design Review (#225)
    * Add termination resistors between P and N signals
    * Add termination resistors on pcb layout on bottom layer
    * Add manufacturing parameters for new resistors
    * Generate output files and bom
    * Switched designator direction on bottom of board, regenerated gerbers and REV folder
    * Regenerated gerbers
    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
    [IO_Converter.SchDoc, IO_Converter_Board_BOM.csv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]
2023-09-19 update issue addressed in #189 for AMDC revision F
    [BackPage.SchDoc]
2023-09-20 update issue address in #227 for AMDC Rev F
    [AMDC.PrjPCB, DriveInterface.SchDoc]
2023-09-25 add 4 array resistor for addressing issue #226
    [AMDC.SchLib, GPIO.SchDoc]
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2023-09-27 add part link for 4 resistor array (#226)
    [GPIO.SchDoc]
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2023-10-11 add picozed symbol and update the values for capacitor having same part number
    [AMDC.SchLib, AnalogADCs.SchDoc, AnalogConditioning.SchDoc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]
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2023-11-03 add correct part number to picoZed board
    [BOM_RevF.csv, BackPage.SchDoc]
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2024-01-31 Update TestBoard generated files (#235)
    * Move testboard BOM to csv file and fix image links
    * Fix images
    [TestBoard_BOM.csv, TestBoard_BOM.xls]
2024-02-12 Replace obsolete BNC part with alternative
    [TestBoard_BOM.csv]
2024-03-27 Update silkscreen and CHANGELOG for REV F (#240)
    * Update label on REV F silkscreen and regenerate outputs
    * Update CHANGELOG.md for REV F
    * Revise changelog messages
    * Revise changelog for #227
    * Update REV E and REV F PCB 3D captures to white background
    ---------
    [AMDC.PrjPCB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]
2025-03-01 AMDC uInverter REVC BOM update (#248)
    * add insulating kit components to uinverter revc bom
    * remove additional designator for R1A, R1B...
    * add mechanical components header to revc bom and organizes parts accordingly
    * fixe csvlint illegal double quotations
    * changes formatting for the mechanical components header
    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
    [uInv_revC_BOM.csv]
2025-04-15 Update AMDC REV20231005F to follow dash-case file name convention (#252)
    * rename the files in the REVF folder to follow dash-case naming
    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
    [BOM_RevF.csv, Pick Place for Rev_F.csv, bom-rev-f.csv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]
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2025-05-16 Update Kaman IO converter board release files to be compliant with new template (#259)
    * update kaman filenames
    * update kaman README
    * update kaman bom
    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
    [IO_Converter.SchDoc, IO_Converter.SchLib, IO_Converter_Board_BOM.csv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]
2025-05-17 Fix Kaman REVC Double Mention and Part Numbers (#265)
    * Fix double mention in rev c folder
    * Remove 1 from bom columns
    * Remove extra line from BOM
    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
    [IO_Converter.SchDoc, IO_Converter.SchLib, io-converter-board-bom.csv]
2025-05-25 Update uInverter Release Files (#261)
    * updates the naming and removes the image in the revc sub folder
    * initial readme changes
    * updates assembly details
    * bom and assembly details update
    * generated BOM and modified BOM
    * makes altium generated BOM 'beautiful and searchable'
    * adds odb, pcb-layers, 3d pdf, and mechanical components to the schematic
    * adds altium generated BOM and mechanical components to schematic library
    * gets rid of weird symbols
    * updates the schematic pdf
    * removes duplicate pcb layers pdf
    * displays designators of mechanical components
    * reverts changes to the altium folder
    * fixes typo...
    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
    [Backpage.SchDoc, Half_bridge_load.SchDoc, Schlib_uInverter.SchLib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]

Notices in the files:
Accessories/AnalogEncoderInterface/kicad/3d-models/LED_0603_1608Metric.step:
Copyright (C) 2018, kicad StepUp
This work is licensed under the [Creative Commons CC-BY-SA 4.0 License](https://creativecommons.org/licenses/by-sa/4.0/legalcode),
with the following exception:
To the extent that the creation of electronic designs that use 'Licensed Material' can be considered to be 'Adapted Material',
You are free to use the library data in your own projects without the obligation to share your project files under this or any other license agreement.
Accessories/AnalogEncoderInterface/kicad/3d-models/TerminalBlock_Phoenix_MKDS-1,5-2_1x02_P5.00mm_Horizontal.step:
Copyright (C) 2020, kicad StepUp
